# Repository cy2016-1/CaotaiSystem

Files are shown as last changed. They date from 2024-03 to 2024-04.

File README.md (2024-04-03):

# CaotaiSystem

### 介绍
一只会走路、会跳舞、会写字的草太椅子     
[视频介绍求三连](https://www.bilibili.com/video/BV1XD42157Rq/)     

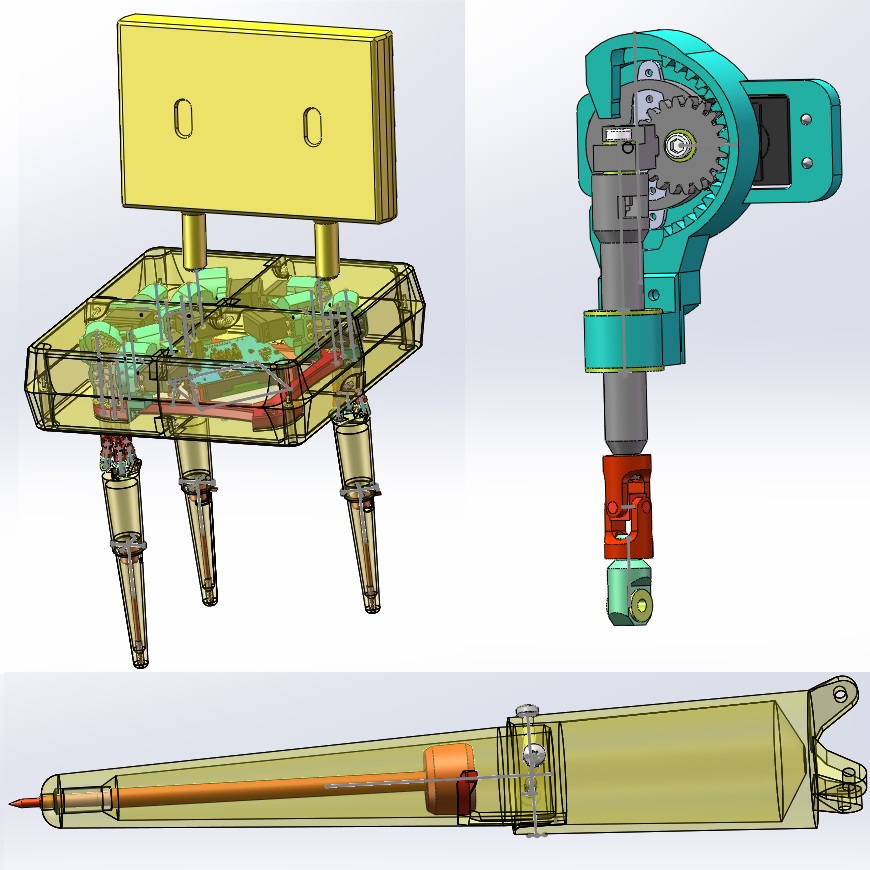
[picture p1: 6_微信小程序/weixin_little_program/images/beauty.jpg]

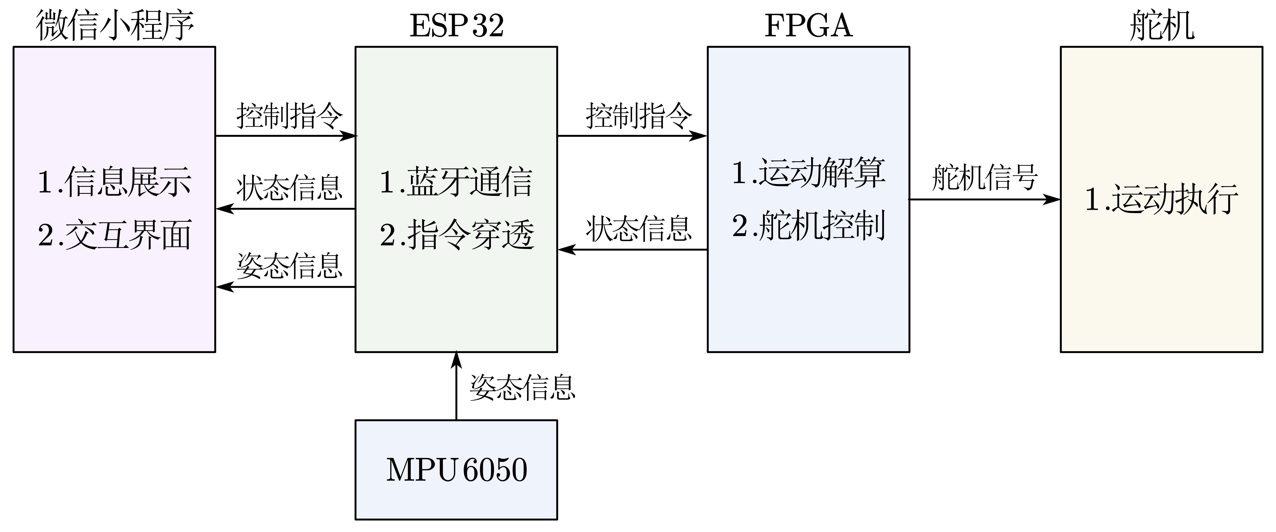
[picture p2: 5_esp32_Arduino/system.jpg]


### 文件内容

##### 1_结构

这个文件夹里放了草太椅子机械结构相关的文件
1.  `草太椅子`文件夹是椅子主体，使用SOLIDWORKS Premium 2021 SP5.0绘制，考虑到Solidworks向下兼容，所以应该使用同版本或更高版本打开
2.  `鞋子`文件夹放了三种鞋子，如果是走路功能，则使用`鞋子-前脚`和`鞋子-后脚`，如果是写字功能和跳舞功能，则换用`后脚-稳定站立`，因为稳定站立版本不容易前倾，所以摔倒风险会小一些，但是走路时难以向前移动重心
3.  `单轴往复运动STL`放了单轴往复子装配体的STL文件，可用于3D打印切片
4.  除了3D打印件以外，还要购买舵机、滑动轴承、肩轴螺丝等标准件，[草太结构标准件BOM.xlsx](1_结构/草太结构标准件BOM.xlsx)是物料清单

##### 2_电路

这个文件夹里放了电路板相关的文件
1.  `ProProject_caotai_ctrl_v2.epro`是嘉立创EDA pro另存为本地的工程文件，嘉立创EDA挺好用的，我已经从Cadence转到国产EDA了。打开步骤如下：     
（1）进入https://lceda.cn/ ，微信扫码登录     
（2）依次点开嘉立创EDA 编辑器 专业版，进入在线编辑器界面     
（3）点击文件->导入->嘉立创EDA专业版，在弹出的文件选择窗口选择`ProProject_caotai_ctrl_v2.epro`     
（4）等待导入完成，1分钟左右     
（5）在弹出的导入窗口中点击保存按钮，即可导入完成     
（6）点开PCB1，屏幕右上角有个类似购物车的图标，点击可以进入打样，下单之前别忘了领取1-4层板沉金免费券
2.  `草太控制板-电子元器件BOM.xlsx`是物料清单，都是正确的，大胆购买吧
3.  舵机不是纯阻性器件，会产生过冲电流，二极管`D2`和`D3`是瞬态抑制二极管，焊接时不可省略它们（血泪教训）

##### 3_算法

这个文件夹里放了算法相关的代码，是用了2个相互独立的全连接神经网络     
已知我们的草太椅子有4条腿，每条腿有3个伸缩连杆，我们算法的目的是解算出某个单腿姿态下3只伸缩连杆的高度，因为针对单条腿进行解算，没有把4条腿都联结起来，所以动作会有些生硬(T.T)     
第一个神经网络是2-64-64-2的结构，输入的2个神经元分别代表草太腿的外倾角和旋转角，输出的2个神经元分别代表伸缩连杆B、C和伸缩连杆A的高度之差     
第二个神经网络是3-64-64-64-3的结构，输入的3个神经元分别代表草太脚尖的x/y/z轴坐标，输出的3个神经元分别代表3只伸缩连杆的高度
1.  [dataset_angle.m](3_算法/dataset_angle.m)和[dataset_draw.m](3_算法/dataset_draw.m)分别用于生成上述两个神经网络的数据集，数据集是通过解方程组产生的，核心代码在[function_forward.m](3_算法/function_forward.m)里面
2.  [train_angle.ipynb](3_算法/train_angle.ipynb)和[train_draw.ipynb](3_算法/train_draw.ipynb)是训练这两个神经网络的代码，用到了`Tensorflow`框架
3.  [eval_angle.m](3_算法/eval_angle.m)和[eval_draw.m](3_算法/eval_draw.m)用于评估这两个神经网络的精度，包括浮点精度和在FPGA实现时的定点精度
4.  [make_para_rom.m](3_算法/make_para_rom.m)、[make_h2t_rom.m](3_算法/make_h2t_rom.m)和[make_sin_rom.m](3_算法/make_sin_rom.m)用于FPGA实现时生成相关的查找表文件

##### 4_FPGA

这个文件夹里放了FPGA的工程，使用安路FPGA开发工具[TD4.6.4](https://www.anlogic.com/support/tools-downloads)进行开发

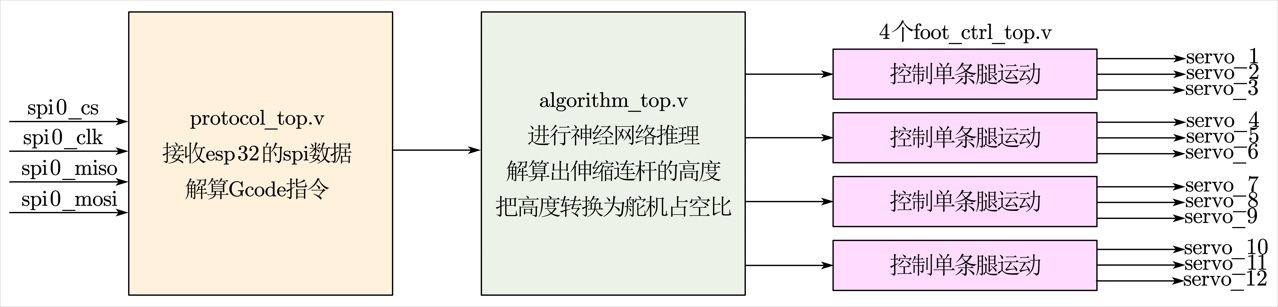
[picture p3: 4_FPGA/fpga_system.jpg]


##### 5_esp32_Arduino

这个文件夹里放了esp32的代码，主要完成2个功能：a.把从蓝牙收到的指令透传给FPGA；b.读取`mpu6050`的姿态
1.  使用`VS code`作为开发环境，`Arduino`作为框架来开发esp32
2.  在`PIO Home`新建工程，板卡选择`Espressif ESP32 Dev Module`，框架选择`Arduino`
3.  在`PIO Home`搜索`mpu6050`，在搜索到的库中选择`I2Cdevlib-MPU6050 by Jeff Rowberg`，add to project
4.  把本文件夹里的`main.cpp`作为工程的主函数编译、下载即可

##### 6_微信小程序

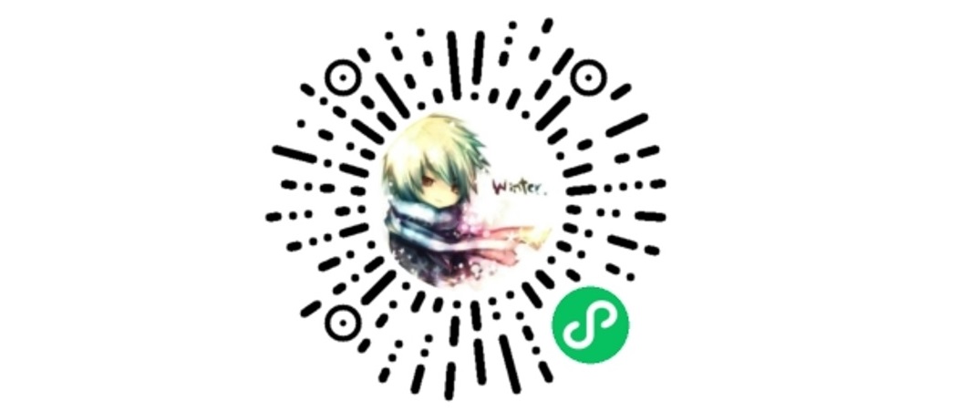
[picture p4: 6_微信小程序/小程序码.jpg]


草太椅子采用微信小程序作为上位机来进行控制，有3种方法打开
1.  微信首页搜索`上仙的蓝牙法器`即可在搜索的小程序结果中找到对应小程序
2.  扫描上面的小程序码可以进入小程序，我这个小程序已经走完ICP备案、微信认证、隐私合规流程了哦，是有编制的小程序哦
3.  把代码下载到本地，然后使用`微信开发者工具`自行编译，使用`真机调试`功能也可体验小程序

### 复刻说明

##### 如果你想完全复刻

1.  如果你想复刻这把椅子，建议从`单轴往复装配体`开始，该装配体实现了单轴的直线运动     
（1）采用了多处`滑动轴承`+`肩轴螺丝`+`M2.5螺母`的设计，安装时一只手用尖嘴钳夹紧`M2.5螺母`，另一只手用六角匙拧`肩轴螺丝`，注意拧得太紧会导致无法运动，拧得太松会导致公差过大，拧到连接处可以转动但又不会乱晃为止     
（2）安装舵机时，应把舵机调整到90°状态，必须把内齿轮安装在整个伸缩连杆行程的中间位置     
（3）3D打印时`伸缩连杆`卧倒打印，这样会使打印的层纹平行于连杆，从而增加结构强度，如果强度太弱会导致和万向节连接处发生断裂
2.  接下来是制作`草太的腿`装配体，把`新的小腿`、`大腿`、`腿的按钮`、`0.5*6*25弹簧`、`花枝俏毛笔`组装在一起
3.  `单轴往复装配体`和`草太的腿`调试完成后，把`十二轴连接器`打印出来，安装在一起，构成草太椅子的主体

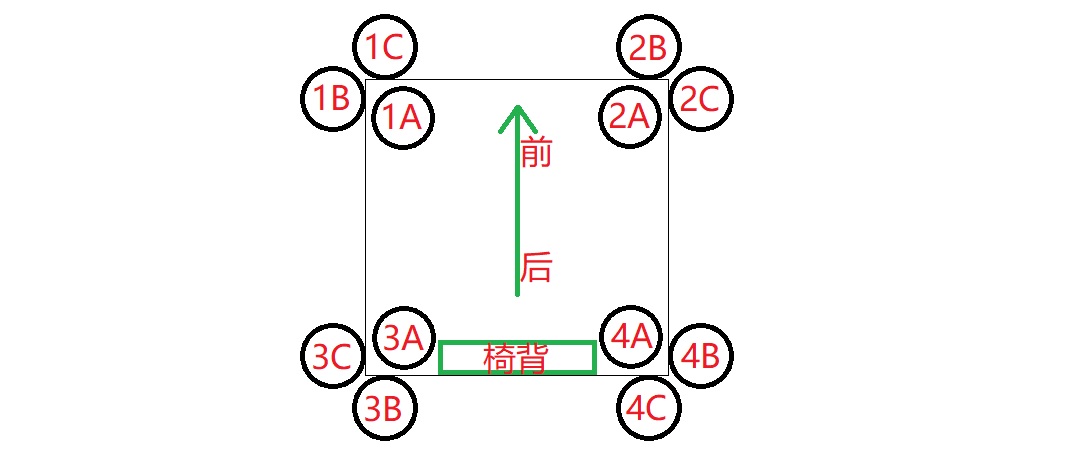
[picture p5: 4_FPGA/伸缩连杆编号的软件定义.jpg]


4.  电路板打样，esp32和FPGA程序烧录，把舵机出线插在电路板上，插线定义参见上图
5.  打印`椅子的顶面`、`椅子的底面`和`椅背`，这三个零件边长30cm左右，如果你的打印机没有这么大，可以把它切分成4块分别打印，然后用螺丝紧固在一起，把上述零件组装在一起，至此结构和电路部分完成
6.  校正！这是最重要的一步，因为即使同一家购买的同一批生产的舵机也难以做到完全一致，所以安装完成后需要手动校正，包括2个层面的校正     
（1）第一个层面是舵机级别的校正，通过不断调整[caotai_top.v](4_FPGA/caotai_v1_0_TangPrimer_EG4S20BG256/rtl/caotai_top.v)第99~110行BIAS参数，最终实现草太上电时4只脚都完全垂直于地面     
（2）第二个层面是整机级别的校正，通过调整微信小程序控制页面的`行走功能超参数`和`跳舞功能超参数`，最终实现草太可以稳定走路和跳舞而不摔倒
7.  最后，enjoy it!

##### 如果你想不完全复刻

1.  虽然完全按照本仓库的代码和图纸复刻出来这把草太椅子很有趣，但可能不适合所有人，甚至会因为我本人水平有限而限制到复刻者的发挥
2.  所以复刻者可以充分发挥自己的能力，对本设计进行魔改，从而提升性能，这也是开源社区存在的意义之一，我目前能想到的有以下几个方向：     
（1）结构方面，把电机改为步进电机，替换掉模拟舵机，模拟舵机的精度太差了     
（2）算法方面，把4条腿联动起来进行运动解算，从而使动作更加自然     
（3）算法方面，把mpu6050的姿态数据用于保持平衡，从而增加稳定性（目前已经可以把数据读出来并上传到小程序显示，但是没有进行处理）     
（4）电路和FPGA方面，替换掉已经停产的[Tang Primer](https://wiki.sipeed.com/hardware/zh/tang/Tang-primer/index.html)，使用在产的其他FPGA核心板，比如载有高云FPGA的[Tang Primer 20K](https://wiki.sipeed.com/hardware/zh/tang/tang-primer-20k/primer-20k.html)，注意核心板替换了以后PCB也要重新绘制哦     
（5）校正流程方面，目前进行舵机层面的校正时，每次都要修改`caotai_top.v`再重新编译下载FPGA固件，这太麻烦了，所以可以通过增加通信协议指令来在线校正     
（6）其他我没有想到的方向...
3.  至少你得把`单轴往复装配体`复刻出来，它的直线运动很有趣

##### 如果你不想复刻

1.  esp32和微信小程序采用蓝牙进行交互的部分，目前已经调试稳定，可以成为其他设计的参考
2.  去B站对应[视频](https://www.bilibili.com/video/BV1XD42157Rq/)下面给我点个一键三连吧

### 参考引用

1.  内摆线实现旋转运动转直线运动的原理参考了[这个视频](https://www.bilibili.com/video/BV1mZ4y1f7oy/)
2.  esp32和微信小程序通过蓝牙进行通信参考了[这个视频](https://www.bilibili.com/video/BV1oq4y1q7sC/)

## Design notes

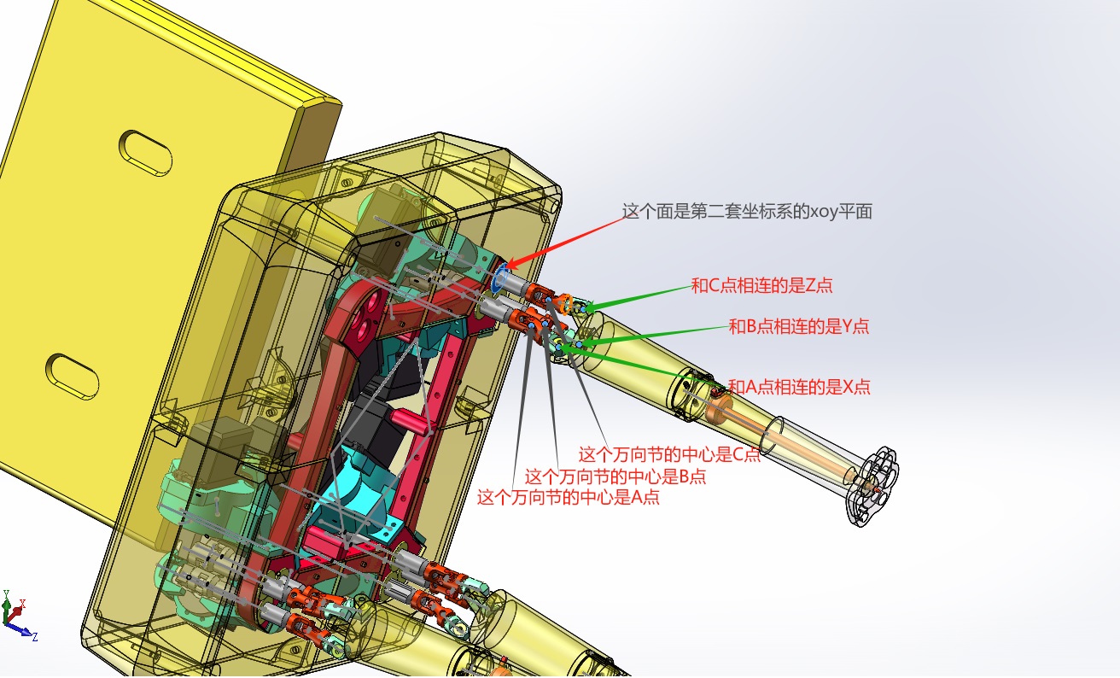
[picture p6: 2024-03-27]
3_算法/点和坐标系定义.jpg

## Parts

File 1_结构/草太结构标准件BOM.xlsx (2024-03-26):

B站 镇元上仙
会动的椅子——草太——结构标准件——Bill of Material
序号 | 在Solidworks中的零件名称 | 购买链接 | 备注 | 单价（￥） | 数量 | 小计（￥）
1 | 大舵机装配体[阿奇设计分享提供]2018 | https://item.taobao.com/item.htm?_u=k2gd4l1n6218&id=561100287559&skuId=3895267604718 | MG996（180度） 从Solidworks里来看似乎“人字-外齿轮-下半部分”零件和舵机有干涉，但请不要担心，因为这家的舵机伸出来的齿比其他家高1mm，你直接打印是正常安装的。 反而，如果你是从其他家买的MG996舵机，有可能需要把“人字-外齿轮-下半部分”零件的最后一个拉伸特征压缩掉才能正常安装 | 11.3 | 12 | 135.6
2 | 易格斯轴承GFM-0304-03 2018 | https://item.taobao.com/item.htm?_u=k2gd4l1nc5a5&id=521900618739&skuId=4980660613011 | 【深灰色.GFM-0304-03】 | 1.4 | 96 | 134.4
3 | 易格斯轴承GFM-1012-06 2018 | https://item.taobao.com/item.htm?_u=k2gd4l1nc5a5&id=521900618739&skuId=4471247887801 | 【深灰色.GFM-1012-06】 | 1.9 | 24 | 45.6
4 | ￠4×M2.5×12 轴肩螺丝 2018 | https://detail.tmall.com/item.htm?_u=k2gd4l1n0a79&id=707426540596&skuId=4973875173715 | 光杆3*12*M2.5(10个) 实际上件48只 | 3.06 | 5 | 15.3
5 | GB／T6172．2-2000非金属嵌件六角锁紧薄螺母2.5 | https://detail.tmall.com/item.htm?_u=k2gd4l1neae7&id=40325857988&skuId=4936608260655 | M2.5(50个)304 实际上件48只 | 6.44 | 1 | 6.44
6 | 万向节6x6装配体 | https://item.taobao.com/item.htm?_u=k2gd4l1n025f&id=521191969211&skuId=3105568646917 | 6*6MM万向节 | 2.8 | 12 | 33.6
7 | GB845-1985十字槽盘头自攻螺钉-C型ST2．9×12 | https://detail.tmall.com/item.htm?_u=k2gd4l1ne507&id=626324857641&skuId=5310338114487 | M3*12【50只】 实际上件98只 | 2.5 | 2 | 5
8 | GB／T70．1-2000内六角圆柱头螺钉M3×12 | https://detail.tmall.com/item.htm?_u=k2gd4l1n1d74&id=634243832662&skuId=5440040927616 | M3*12（50个 实际上件12只 | 2.53 | 1 | 2.53 | 草太椅面的边长约30cm，而我的打印机最大只能打印20cm，所以我就把椅面分成了4块分别打印然后再用螺钉螺母拼接起来 这组螺钉螺母就是拼接椅面的4个part用的，如果你的打印机大于30厘米，这个就可以省掉啦
9 | GB／T6172．2-2000非金属嵌件六角锁紧薄螺母3 | https://detail.tmall.com/item.htm?_u=k2gd4l1neae7&id=40325857988&skuId=4936608260656 | M3(50个)304 实际上件12只 | 3.24 | 1 | 3.24
10 | 大的压缩的弹簧 | https://detail.tmall.com/item.htm?_u=k2gd4l1n5679&id=640992562746&spm=a1z09.2.0.0.67002e8dteUE9g | 0.5*6*25mm 需要口头告诉客服这个尺寸，是定制的 | 4.5 | 1 | 4.5
11 | 笔芯 | https://detail.tmall.com/item.htm?_u=k2gd4l1n70f1&id=601808839108&skuId=4206044776631 | 花枝俏（小） | 6.6 | 1 | 6.6 | 本来想用按动笔笔芯的，但是公差太大无法演示写字功能，所以换成了软软的毛笔
12 | 椅背 | https://item.taobao.com/item.htm?_u=k2gd4l1n191b&id=38828402808&skuId=5209399448081 | 黄30*17*4.5厘米2张 草太4条腿站立没问题，但是如果抬起后面的一条腿，就会因为3D打印的椅背太重而重心太靠后而摔倒，所以在演示跳舞功能和走路功能时我把3D打印的椅背换成了泡沫椅背，从而减小了重量，减小了保持平衡的难度 | 16 | 1 | 16
13 |  |  |  |  | 总计 | 408.81 | RMB
14
15
16
17
18
19
20
21
22
23
24
25
26
27

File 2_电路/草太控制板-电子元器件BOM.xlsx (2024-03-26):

No. | Quantity | Designator | Comment | 购买链接 | 备注 | 单价￥ | 小计￥
1 | 7 | C1,C2,C9,C13,C14,C23,C40 | 47uF | https://item.taobao.com/item.htm?_u=l2gd4l1n249c&id=651730279981&skuId=4866792818122 | 47UF 25V尺寸：0603（100只） | 0.1 | 0.7
2 | 11 | C3,C10,C15,C22,C24,C26,C31,C36,C38,C41,C42 | 10uF | https://item.taobao.com/item.htm?_u=l2gd4l1n249c&id=651730279981&skuId=4866792818110 | 10UF 25V尺寸：0603（100只） | 0.04 | 0.44
3 | 13 | C4,C5,C11,C16,C17,C21,C25,C27,C30,C34,C35,C37,C39 | 0.1uF | https://item.taobao.com/item.htm?_u=l2gd4l1n175a&id=568023887250&skuId=3790413719806 | 0，1UF 104 | 0.04 | 0.52
4 | 2 | C6,C18 | 2.2nF | https://detail.tmall.com/item.htm?_u=l2gd4l1nf8c8&id=611226763970&skuId=4468071918326 | 0603 2.2NF ±10% 50V（50只） | 0.04 | 0.08
5 | 2 | C7,C19 | 22pF | https://detail.tmall.com/item.htm?_u=l2gd4l1nb44e&id=610747185789&skuId=4300586341508 | 0603 22PF 5% 50V（50只） | 0.08 | 0.16
6 | 2 | C8,C20 | 0.01uF | https://item.taobao.com/item.htm?_u=l2gd4l1n175a&id=568023887250&skuId=3790413719805 | 0，01UF 103 | 0.04 | 0.08
7 | 1 | C12 | 470uF | https://detail.tmall.com/item.htm?_u=l2gd4l1nbf3d&id=608506860246&skuId=4449283259604 | 470UF 50V绿金高频10*20 10只 | 0.38 | 0.38
8 | 1 | C28 | 1uF | https://item.taobao.com/item.htm?_u=l2gd4l1n249c&id=651730279981&skuId=4866792818086 | 1UF 50V尺寸：0603（100只） | 0.04 | 0.04
9 | 3 | D1,D2,D3 | SMBJ24CD-M3/I | https://detail.tmall.com/item.htm?_u=l2gd4l1nb88d&id=709925638952&skuId=5148547086648 | SMBJ6.5A/KK单向（20个） | 0.09 | 0.27
10 | 2 | H3,H4 | HDR-F_2.54_1x20P | https://detail.tmall.com/item.htm?_u=l2gd4l1nde67&id=607373839301&skuId=4255759944279 | 20P单排（10只） | 0.25 | 0.5
11 | 4 | H5,H6,H7,H8 | HDR-M_2.54_2x6 | https://detail.tmall.com/item.htm?_u=l2gd4l1n6acf&id=613869696323&skuId=4324124816160 | 2*6P 直针 铜（20条） | 0.16 | 0.64
12 | 1 | H9 | B-2100S08P-A110 | https://detail.tmall.com/item.htm?_u=l2gd4l1nad2a&id=615605943029&skuId=5048123656390 | MPU6050模块 黄色钽电容 镀金板 | 8.8 | 8.8
13 | 2 | L1,L2 | 4.7uH | https://detail.tmall.com/item.htm?_u=l2gd4l1n014e&id=607797277916&skuId=4265923664938 | CDRH104R 4.7UH(4R7) 5只 | 0.4 | 0.8
14 | 2 | Q1,Q2 | SS8050-H | https://detail.tmall.com/item.htm?_u=l2gd4l1n1e24&id=621537643738&skuId=4693769020834 | SS8050 SOT23 印字Y1 贴片（50个） | 0.02 | 0.04
15 | 2 | R1,R6 | 100K | https://detail.tmall.com/item.htm?_u=l2gd4l1nbe1d&id=529532295464&skuId=3924853511284 | 100K 1% （100个） | 0.03 | 0.06
16 | 4 | R2,R3,R7,R8 | 43K | https://detail.tmall.com/item.htm?_u=l2gd4l1nbe1d&id=529532295464&skuId=4880421480034 | 43K 1% （100个） | 0.03 | 0.12
17 | 5 | R4,R9,R11,R12,R13 | 10K | https://detail.tmall.com/item.htm?_u=l2gd4l1nef42&id=692806644853&skuId=4923889453118 | 0603 10K（100只） | 0.02 | 0.1
18 | 2 | R5,R10 | 1.6K | https://detail.tmall.com/item.htm?_u=l2gd4l1nef42&id=692806644853&skuId=4923889453092 | 0603 1.6K（100只） | 0.02 | 0.04
19 | 2 | R14,R15 | 5.1K | https://detail.tmall.com/item.htm?_u=l2gd4l1nef42&id=692806644853&skuId=4923889453108 | 0603 5.1K（100只） | 0.02 | 0.04
20 | 2 | R16,R17 | 4.7K | https://detail.tmall.com/item.htm?_u=l2gd4l1nbe1d&id=529532295464&skuId=3924853511210 | 4.7K 1% （100个） 无需上件 | 0.03 | 0.06
21 | 27 | R18,R19,R20,R21,R22,R23,R24,R25,R26,R27,R28,R29,R30,R31,R32,R33,R34,R35,R36,R37,R38,R39,R40,R41,R42,R43,R44 | 22 | https://detail.tmall.com/item.htm?_u=l2gd4l1nbe1d&id=529532295464&skuId=3924853511182 | 22欧 1% (100个) | 0.03 | 0.81
22 | 1 | R45 | 0 | https://detail.tmall.com/item.htm?_u=l2gd4l1n1e36&id=609667022770&skuId=4451493542761 | 0603 0R欧姆1% 100个 无需上件 | 0.03 | 0.03
23 | 1 | U1 | 3节18650电池盒插针 | https://item.taobao.com/item.htm?_u=l2gd4l1n4af0&id=706460008309&skuId=4965677504942 | 3节18650 硬壳 插针 1个 | 3.2 | 3.2
24 | 4 | U2,U5,U7,U16 | 1N5824 | https://detail.tmall.com/item.htm?_u=l2gd4l1nd759&id=14947051899&skuId=4174373459142 | SS54二极管 1N5824 5A/40V DO-214AC/SMA(10个） | 0.39 | 1.56
25 | 1 | U3 | KCD11船型开关 | https://detail.tmall.com/item.htm?_u=l2gd4l1n3c8b&id=529061266965&skuId=3945699927565 | 2脚2档 红色 10x15mm（5个） | 0.46 | 0.46
26 | 2 | U4,U6 | TPS54531DDAR | https://item.taobao.com/item.htm?_u=l2gd4l1n941b&id=569649171844&spm=a1z09.2.0.0.1f7a2e8dEYwB9l | tps54531 | 1.45 | 2.9
27 | 1 | U8 | AMS1117-3V3 | https://detail.tmall.com/item.htm?_u=l2gd4l1n0514&id=13763392732&skuId=4172153575113 | AMS1117-3.3V 封装SOT89（10个） | 0.32 | 0.32
28 | 1 | U9 | ESP32-S | https://item.taobao.com/item.htm?_u=l2gd4l1nd17b&id=634424428305&skuId=4543431189229 | ESP32-WROOM-32E(16MB) | 19.5 | 19.5
29 | 1 | U10 | CH340C | https://item.taobao.com/item.htm?_u=l2gd4l1ndf89&id=575878939854&skuId=5125097058072 | CH340C | 1.65 | 1.65
30 | 1 | U11 | 20009-UCAF001-X | https://detail.tmall.com/item.htm?_u=l2gd4l1n7eec&id=712263210606&skuId=4986402848290 | USB/TYPE-C-16P/不带弹片/高品质(10个） | 0.35 | 0.35
31 | 1 | U15 | AMS1117-5V0 | https://detail.tmall.com/item.htm?_u=l2gd4l1n0514&id=13763392732&skuId=4172153575113 | AMS1117-5.0V 封装SOT89（10个） | 0.32 | 0.32
 |  |  |  |  |  | 总计 | 44.97 | RMB

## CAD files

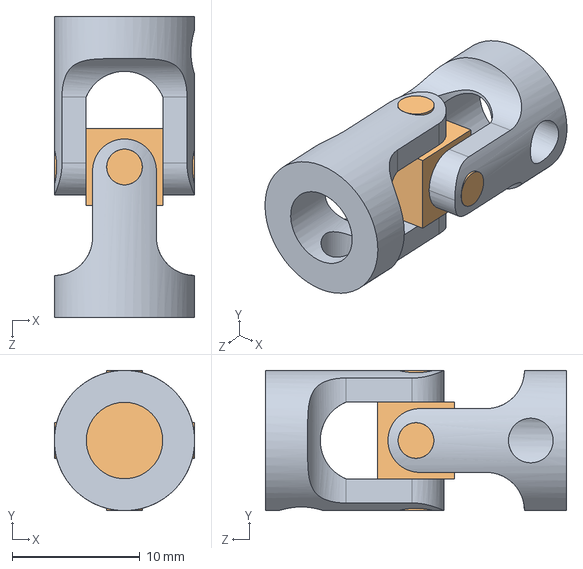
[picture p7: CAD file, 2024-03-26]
1_结构/草太椅子/万向节6x6装配体.SLDASM
11.0 x 11.0 x 23.6 mm
万向节6x6连接件 x 2
万向节6x6中间件

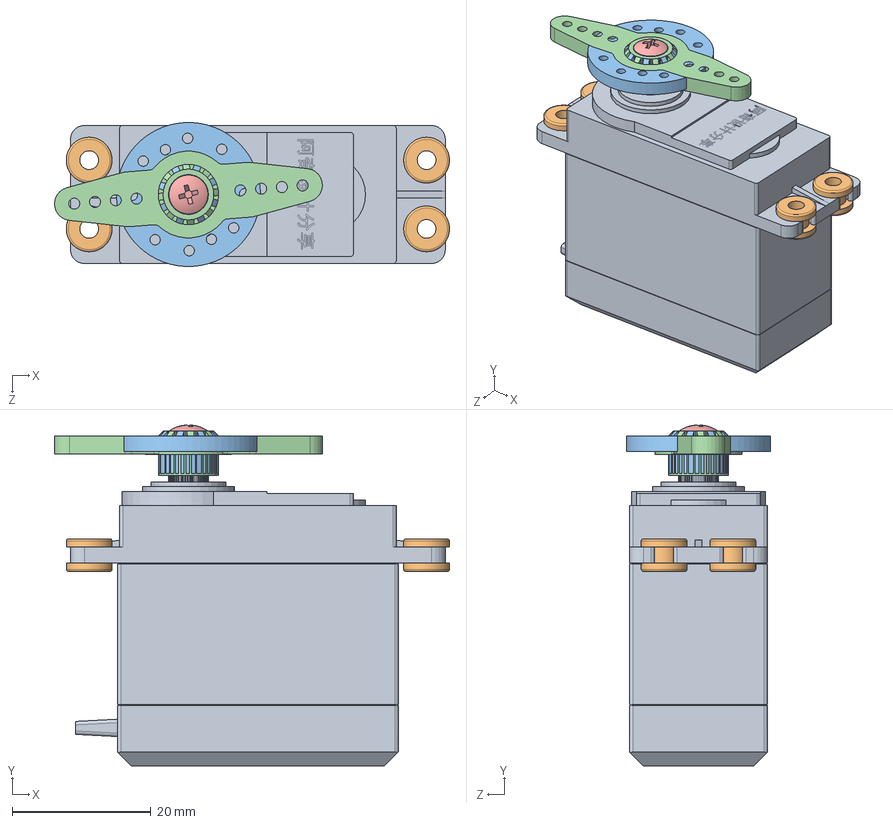
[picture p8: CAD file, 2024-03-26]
1_结构/草太椅子/大舵机装配体[阿奇设计分享提供]2018.SLDASM
56.9 x 49.1 x 20.7 mm
大舵机渲染2018
舵机橡胶圈渲染2018 x 4
舵机圆舵盘渲染2018
舵机单臂舵盘渲染2018
cross recessed pan head screws gb(GB_CROSS_SCREWS_TYPE1 M3X6-6 H type-N)2018

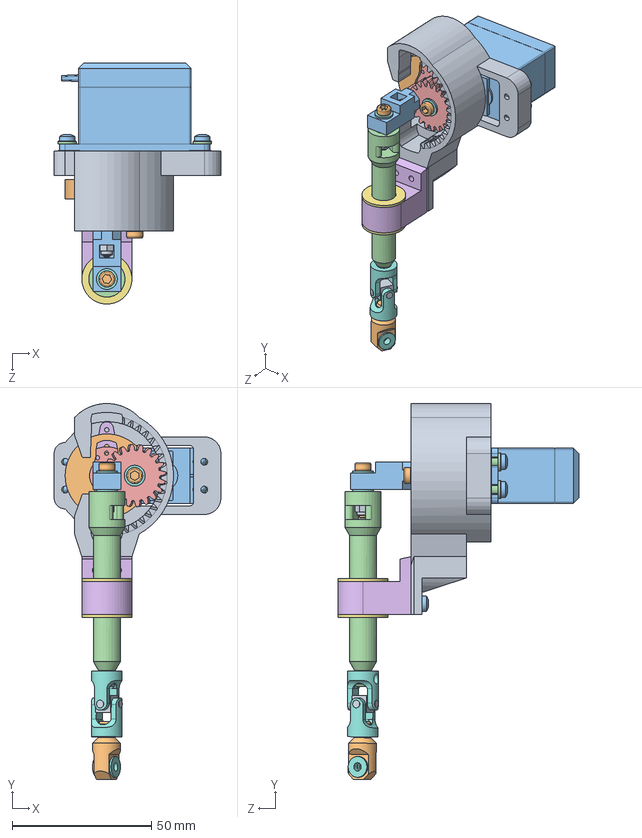
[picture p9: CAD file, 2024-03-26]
1_结构/草太椅子/单臂往复装配体.SLDASM
60.0 x 135.1 x 86.7 mm
人字-外齿轮-下半部分
内外齿轮连杆
大舵机渲染2018
舵机橡胶圈渲染2018 x 4
舵机单臂舵盘渲染2018
cross recessed pan head screws gb(GB_CROSS_SCREWS_TYPE1 M3X6-6 H type-N)2018
易格斯轴承GFM-0304-03 2018 x 8
GB／T6172．2-2000非金属嵌件六角锁紧薄螺母2.5 x 3
￠4×M2.5×12 轴肩螺丝 2018 x 3
直角连杆
伸缩连杆
人字-内齿轮
人字-外齿轮-上半部分
易格斯轴承GFM-1012-06 2018 x 2
万向节6x6连接件 x 2
万向节6x6中间件
大腿连杆
GB845-1985十字槽盘头自攻螺钉-C型ST2．9×12 x 6

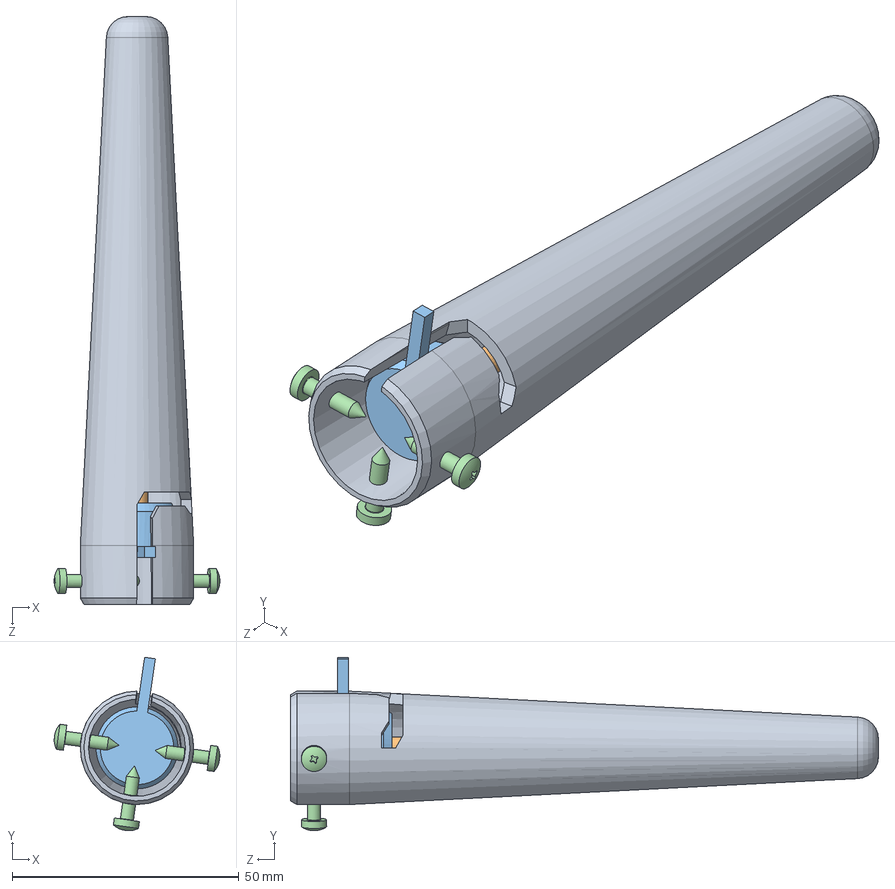
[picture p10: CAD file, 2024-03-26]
1_结构/草太椅子/草太的腿.SLDASM
36.5 x 38.2 x 129.6 mm
新的小腿
笔芯
腿的按钮
GB845-1985十字槽盘头自攻螺钉-C型ST2．9×12 x 3

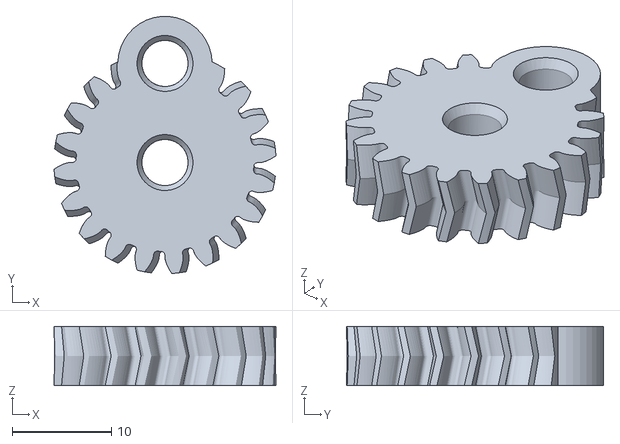
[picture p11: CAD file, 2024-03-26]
1_结构/单轴往复运动STL/人字-内齿轮.STL
22.4 x 25.9 x 6.00

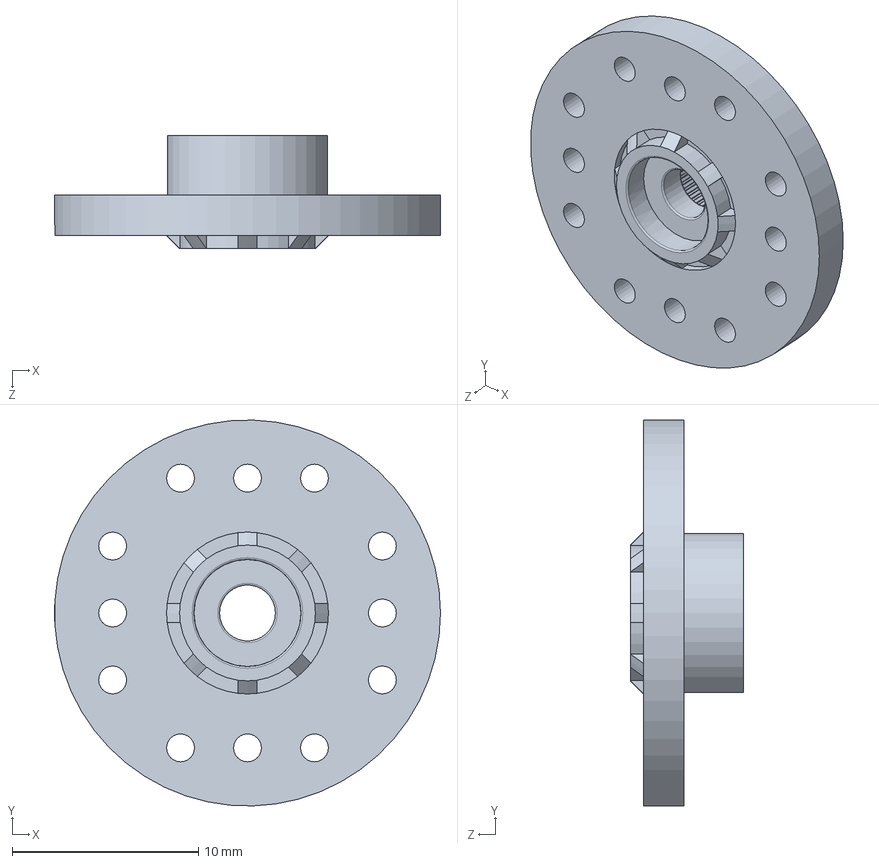
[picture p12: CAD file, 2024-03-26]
1_结构/草太椅子/舵机圆舵盘渲染2018.sldprt
20.8 x 20.7 x 6.10 mm

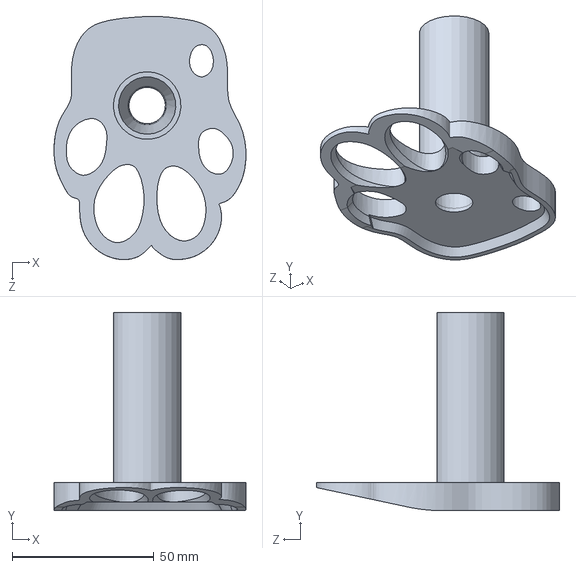
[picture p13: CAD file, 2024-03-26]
1_结构/鞋子/鞋子-后脚.SLDPRT
67.8 x 70.0 x 85.9 mm

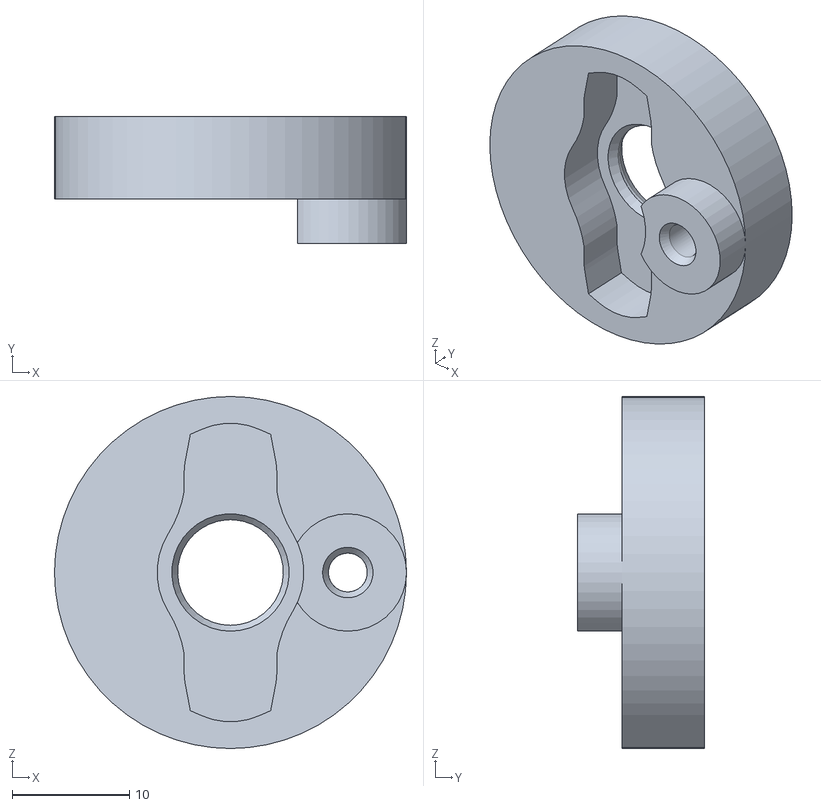
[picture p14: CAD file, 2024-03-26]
1_结构/单轴往复运动STL/内外齿轮连杆.STL
30.0 x 10.8 x 30.0

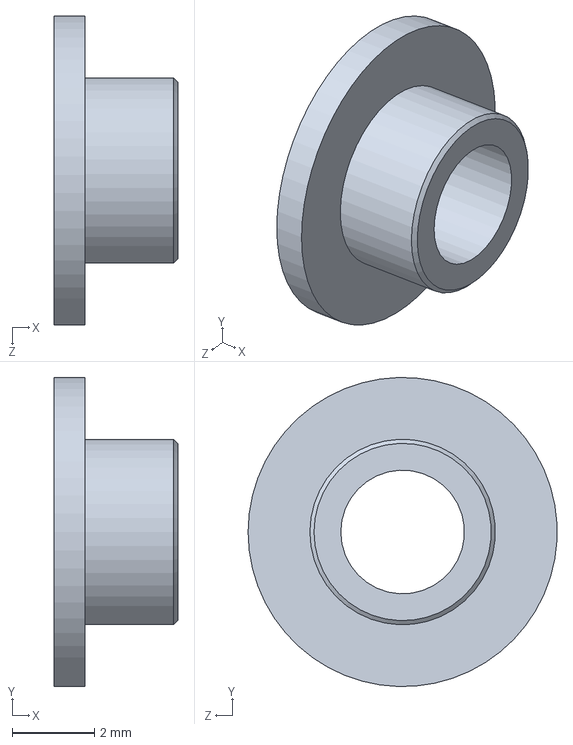
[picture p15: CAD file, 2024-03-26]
1_结构/草太椅子/易格斯轴承GFM-0304-03 2018.SLDPRT
3.00 x 7.50 x 7.49 mm

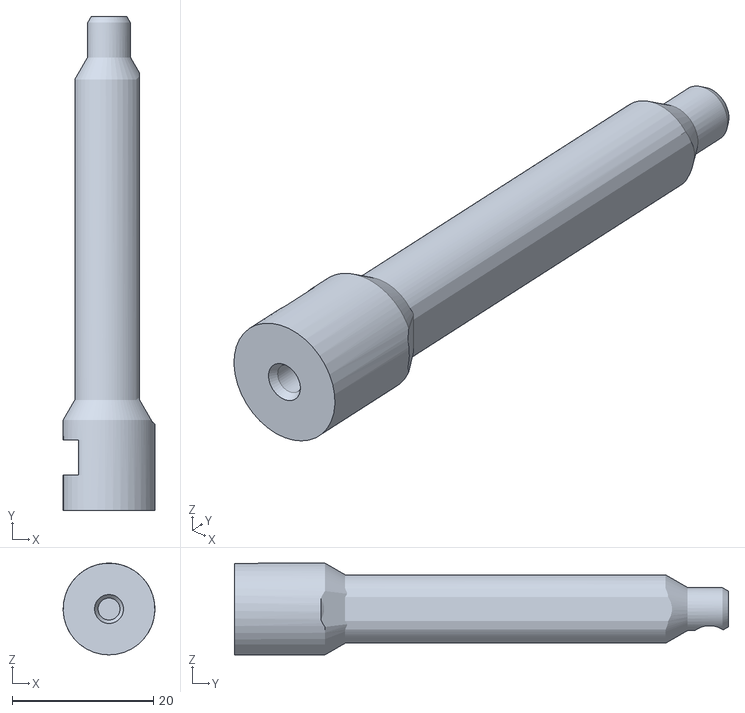
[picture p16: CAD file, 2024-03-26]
1_结构/单轴往复运动STL/伸缩连杆.STL
13.0 x 70.0 x 13.0

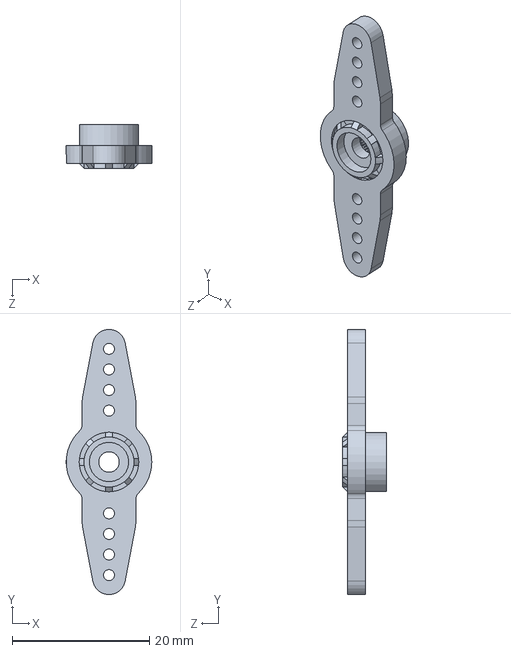
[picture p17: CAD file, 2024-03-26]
1_结构/草太椅子/舵机单臂舵盘渲染2018.sldprt
12.5 x 38.7 x 6.35 mm

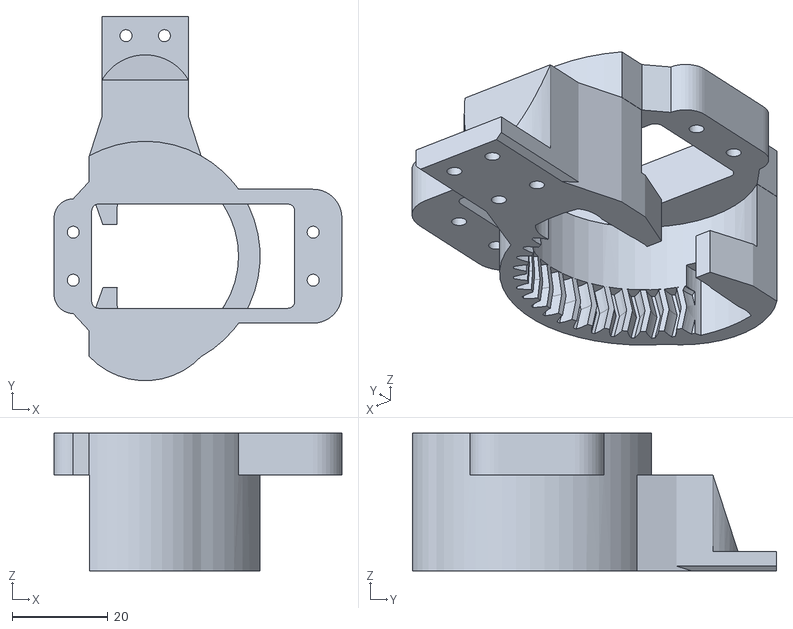
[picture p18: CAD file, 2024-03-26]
1_结构/单轴往复运动STL/人字-外齿轮-下半部分.STL
60.0 x 75.9 x 28.7

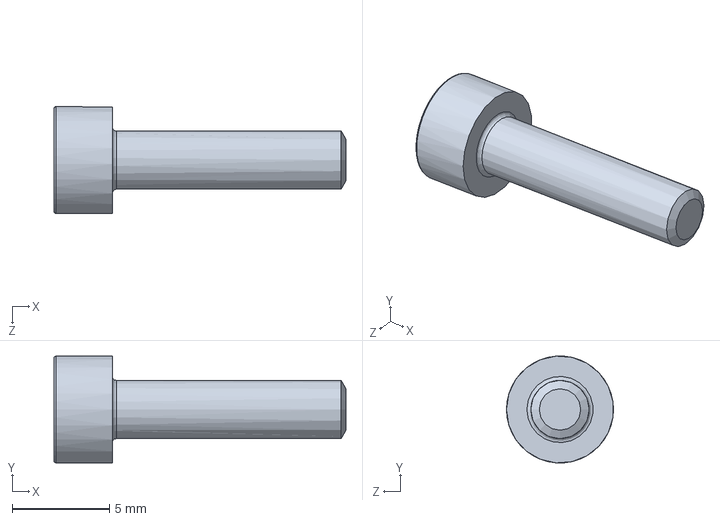
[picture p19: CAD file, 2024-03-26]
1_结构/草太椅子/GB／T70．1-2000内六角圆柱头螺钉M3×12.SLDPRT
15.0 x 5.48 x 5.50 mm

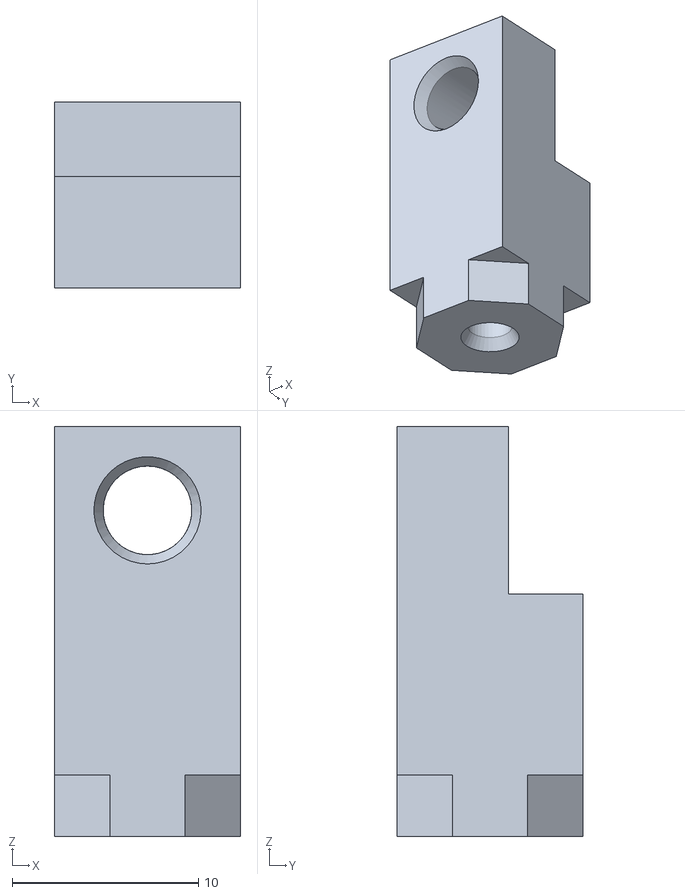
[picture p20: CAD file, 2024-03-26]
1_结构/单轴往复运动STL/直角连杆.STL
10.0 x 10.0 x 22.0

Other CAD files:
1_结构/鞋子/鞋子-后脚-稳定站立.SLDPRT
1_结构/鞋子/鞋子-前脚.SLDPRT
1_结构/草太椅子/易格斯轴承GFM-1012-06 2018.SLDPRT
1_结构/单轴往复运动STL/人字-外齿轮-上半部分.STL
1_结构/草太椅子/GB845-1985十字槽盘头自攻螺钉-C型ST2．9×12.SLDPRT
1_结构/草太椅子/GB／T6172．2-2000非金属嵌件六角锁紧薄螺母2.5.SLDPRT
1_结构/草太椅子/GB／T6172．2-2000非金属嵌件六角锁紧薄螺母3.SLDPRT
1_结构/草太椅子/cross recessed pan head screws gb(GB_CROSS_SCREWS_TYPE1 M3X6-6 H type-N)2018.sldprt
1_结构/草太椅子/万向节6x6中间件.SLDPRT
1_结构/草太椅子/万向节6x6连接件.SLDPRT
1_结构/草太椅子/人字-外齿轮-上半部分.SLDPRT
1_结构/草太椅子/人字-外齿轮-下半部分.SLDPRT
1_结构/草太椅子/伸缩连杆.SLDPRT
1_结构/草太椅子/内外齿轮连杆.SLDPRT
1_结构/草太椅子/十二轴连接器.SLDPRT
1_结构/草太椅子/大的压缩的弹簧.SLDPRT
1_结构/草太椅子/大腿连杆.SLDPRT
1_结构/草太椅子/大腿部件.SLDPRT
1_结构/草太椅子/大舵机渲染2018.sldprt
1_结构/草太椅子/新的小腿.SLDPRT
1_结构/草太椅子/椅子的底面.SLDPRT
1_结构/草太椅子/椅子的底面_partA.SLDPRT
1_结构/草太椅子/椅子的底面_partB.SLDPRT
1_结构/草太椅子/椅子的底面_partC.SLDPRT
1_结构/草太椅子/椅子的底面_partD.SLDPRT
1_结构/草太椅子/椅子的顶面.SLDPRT
1_结构/草太椅子/椅子的顶面_partA.SLDPRT
1_结构/草太椅子/椅子的顶面_partB.SLDPRT
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

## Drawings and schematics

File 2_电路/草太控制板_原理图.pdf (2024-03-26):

# 电池盒

# 第一只TPS54531

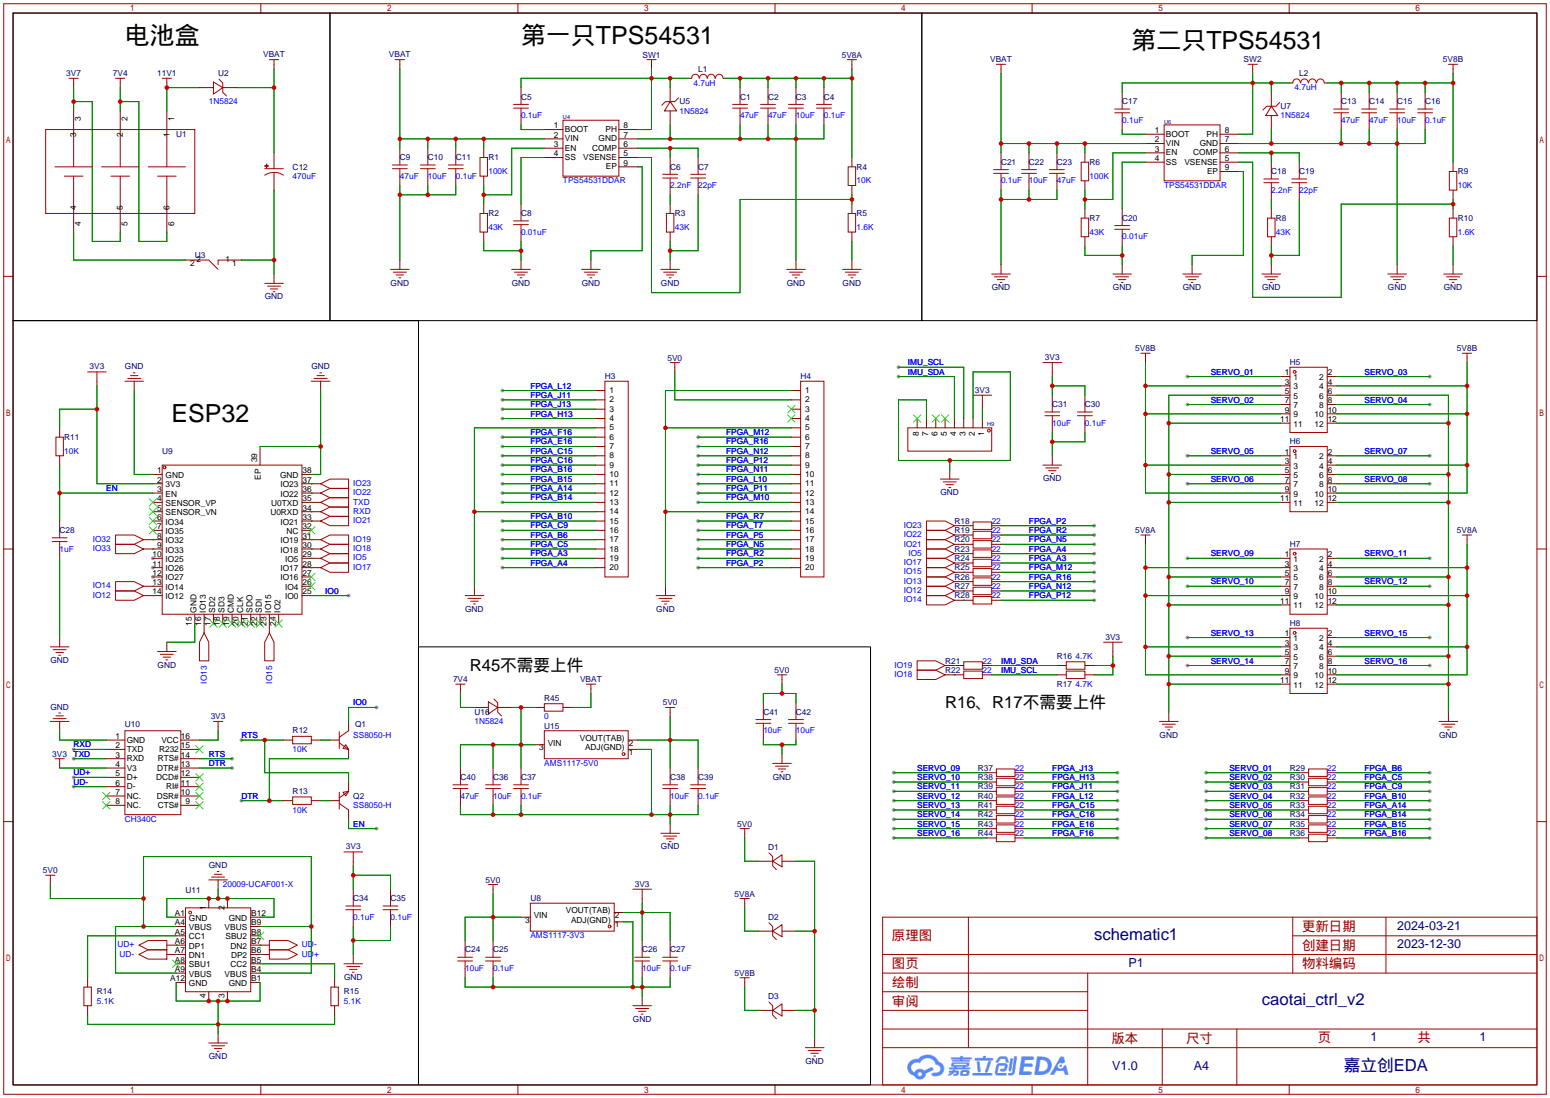
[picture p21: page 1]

GND B1 GND A12 VBUS A9 SBU1 A8 DN1 A7 DP1 A6 CC1 A5 VBUS A4 GND A1

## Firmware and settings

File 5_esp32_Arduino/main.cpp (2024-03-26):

#include <Arduino.h>
#include <BLEDevice.h>
#include <BLEServer.h>
#include <BLEUtils.h>
#include <BLE2902.h>
#include <iostream>
#include <SPI.h>
#include "I2Cdev.h"
#include "Wire.h"
#include "MPU6050_6Axis_MotionApps20.h"
// 宏定义
#define IMU_I2C_SDA 19 
#define IMU_I2C_SCL 18
#define PIN_CS0 15
#define FPGA_RSTN 17
#define FOOT_BACKPRESS 5
#define FOOT_BUSYSTATE 21
#define SERVICE_UUID "12a59900-17cc-11ec-9621-0242ac130002" // UART service UUID
#define CHARACTERISTIC_UUID_RX "12a59e0a-17cc-11ec-9621-0242ac130002"
#define CHARACTERISTIC_UUID_TX "12a5a148-17cc-11ec-9621-0242ac130002"
#define NOTIFY_LEN 10
#define QUEUE_LEN 32768


// BLE things
uint32_t ble_notify_cnt = 0;
uint32_t heartCount = 0;
uint8_t  broadcastValue[NOTIFY_LEN];
BLEServer *pServer = NULL;                   // BLEServer指针 pServer
BLECharacteristic *pTxCharacteristic = NULL; // BLECharacteristic指针 pTxCharacteristic
BLECharacteristic *pRxCharacteristic = NULL;
bool deviceConnected = false;                // 本次连接状态
bool oldDeviceConnected = false;             // 上次连接状态
uint8_t cmd_err_num = 0;
// mpu things
MPU6050 mpu;
bool dmpReady = false;  // set true if DMP init was successful
uint8_t mpuIntStatus;   // holds actual interrupt status byte from MPU
uint8_t devStatus;      // return status after each device operation (0 = success, !0 = error)
uint16_t packetSize;    // expected DMP packet size (default is 42 bytes)
uint16_t fifoCount;     // count of all bytes currently in FIFO
uint8_t fifoBuffer[64]; // FIFO storage buffer
Quaternion q;           // [w, x, y, z]         quaternion container
VectorInt16 aa;         // [x, y, z]            accel sensor measurements
VectorInt16 aaReal;     // [x, y, z]            gravity-free accel sensor measurements
VectorInt16 aaWorld;    // [x, y, z]            world-frame accel sensor measurements
VectorFloat gravity;    // [x, y, z]            gravity vector
float euler[3];         // [psi, theta, phi]    Euler angle container
float ypr[3];           // [yaw, pitch, roll]   yaw/pitch/roll container and gravity vector
uint8_t teapotPacket[14] = { '$', 0x02, 0,0, 0,0, 0,0, 0,0, 0x00, 0x00, '\r', '\n' };


class CircularQueue {
private:
  int front, rear;
  int capacity;
  uint8_t* queue;
public:
  CircularQueue(int k) {
    capacity = k + 1;
    queue = new uint8_t[capacity];
    front = rear = 0;
  }
  void enQueue(uint8_t value) {
    queue[rear] = value;
    rear = (rear + 1) % capacity;
  }
  uint8_t deQueue() {
    uint8_t ddd = queue[front];
    front = (front + 1) % capacity;
    return ddd;
  }
  bool isEmpty() {
    return rear == front;
  }
  bool isFull() {
    return (rear + 1) % capacity == front;
  }
  int getRear() {
    return rear;
  }
  int getFront() {
    return front;
  }
};

// 循环队列初始化
CircularQueue bleQueue(QUEUE_LEN);

class MyServerCallbacks : public BLEServerCallbacks
{
  void onConnect(BLEServer *pServer)
  {
    deviceConnected = true;
  };
  void onDisconnect(BLEServer *pServer)
  {
    deviceConnected = false;
  }
};

class MyCallbacks : public BLECharacteristicCallbacks
{
  void onWrite(BLECharacteristic *pCharacteristic)
  {
    Serial.printf("onWrite\n");
    std::string rxValue = pCharacteristic->getValue(); // 接收信息
    if (rxValue.length() > 0)
    {
      for (int i = 0; i < rxValue.length(); i++) {
        bleQueue.enQueue(rxValue[i]);
      }
    }
  }
};

void notifyWx() {
  int8_t temp = 0;
  if (!dmpReady) return;
  if (mpu.dmpGetCurrentFIFOPacket(fifoBuffer)) {
  mpu.dmpGetQuaternion(&q, fifoBuffer);
  mpu.dmpGetGravity(&gravity, &q);
  mpu.dmpGetYawPitchRoll(ypr, &q, &gravity);
    /*Serial.print("ypr\t");
    Serial.print(ypr[0] * 180/M_PI);
    Serial.print("\t");
    Serial.print(ypr[1] * 180/M_PI);
    Serial.print("\t");
    Serial.println(ypr[2] * 180/M_PI);*/
  }
  heartCount = heartCount + 1;
  for(int i=0;i<4;i++) {
    broadcastValue[NOTIFY_LEN-1-i] = static_cast<uint8_t>((heartCount>>(8*i)) & 255);
  }
  temp = (int8_t)(ypr[2] * 180/M_PI);
  if (temp<0) temp = temp + 256;
  for(int i=4;i<5;i++) {
    broadcastValue[NOTIFY_LEN-1-i] = static_cast<uint8_t>(temp & 255);
  }
  temp = (int8_t)(ypr[1] * 180/M_PI);
  if (temp<0) temp = temp + 256;
  for(int i=5;i<6;i++) {
    broadcastValue[NOTIFY_LEN-1-i] = static_cast<uint8_t>(temp & 255);
  }
  temp = (int8_t)(ypr[0] * 180/M_PI);
  if (temp<0) temp = temp + 256;
  for(int i=6;i<7;i++) {
    broadcastValue[NOTIFY_LEN-1-i] = static_cast<uint8_t>(temp & 255);
  }
  for(int i=7;i<8;i++) {
    broadcastValue[NOTIFY_LEN-1-i] = static_cast<uint8_t>(cmd_err_num);
  }
  Serial.printf("cmd_err_num is %d\n", cmd_err_num);
  for(int i=8;i<9;i++) {
    broadcastValue[NOTIFY_LEN-1-i] = static_cast<uint8_t>((digitalRead(FOOT_BACKPRESS)==1) ? 255 : 0);
  }
  for(int i=9;i<10;i++) {
    broadcastValue[NOTIFY_LEN-1-i] = static_cast<uint8_t>((digitalRead(FOOT_BUSYSTATE)==1) ? 255 : 0);
  }
  pTxCharacteristic->setValue(broadcastValue, NOTIFY_LEN);       // 设置要发送的值
  pTxCharacteristic->notify();              // 广播
}

void clearQueue() {
  if (bleQueue.isEmpty()) return;
  uint8_t ccc = 0;
  //Serial.printf("BLE RECV:");
  digitalWrite(PIN_CS0, LOW);
  while (!bleQueue.isEmpty()) {
    if (digitalRead(FOOT_BACKPRESS)==1) {
      Serial.println("FOOT_BACKPRESS==1");
      //Serial.printf("rear is %d, front is %d\n", bleQueue.getRear(), bleQueue.getFront());
      notifyWx();
      delay(1000);
      break;
    }
    ccc = bleQueue.deQueue();
    cmd_err_num = SPI.transfer(ccc);
    //Serial.printf("%c", ccc);
  }
  //Serial.println();
  digitalWrite(PIN_CS0, HIGH);
}

void serialISP() {
  uint8_t ccc = 0;
  if (Serial.available()>0) {
    Serial.printf("UART RECV:");
    digitalWrite(PIN_CS0, LOW);
    while (Serial.available()>0) {
      ccc = Serial.read();
      cmd_err_num = SPI.transfer(ccc);
      Serial.printf("%c", ccc);
    }
    Serial.println();
    digitalWrite(PIN_CS0, HIGH);
  }
}

void bleLoop() {
  // deviceConnected 已连接
  if (deviceConnected)
  {
    notifyWx();
  }
  // disconnecting  断开连接
  if (!deviceConnected && oldDeviceConnected)
  {
    delay(500);                  // 留时间给蓝牙缓冲
    pServer->startAdvertising(); // 重新广播
    Serial.println("BLE Restart Advertising");
    oldDeviceConnected = deviceConnected;
  }
  // connecting  正在连接
  if (deviceConnected && !oldDeviceConnected)
  {
    Serial.println("BLE Connect Successfully");
    // do stuff here on connecting
    oldDeviceConnected = deviceConnected;
  }
}

void bleSetup() {
  // 创建一个 BLE 设备
  BLEDevice::init("UART_BLE");
  // 创建一个 BLE 服务
  pServer = BLEDevice::createServer();
  pServer->setCallbacks(new MyServerCallbacks()); // 设置回调
  BLEService *pService = pServer->createService(SERVICE_UUID);
  // 创建一个 BLE 特征
  pTxCharacteristic = pService->createCharacteristic(CHARACTERISTIC_UUID_TX, BLECharacteristic::PROPERTY_NOTIFY);
  pTxCharacteristic->addDescriptor(new BLE2902());
  pRxCharacteristic = pService->createCharacteristic(CHARACTERISTIC_UUID_RX, BLECharacteristic::PROPERTY_WRITE);
  pRxCharacteristic->setCallbacks(new MyCallbacks()); // 设置回调
  // BLE开始
  pService->start();                  // 开始服务
  pServer->getAdvertising()->start(); // 开始广播
  Serial.println("BLE OK... ");
}

void mpuSetup() {
  Wire.begin(IMU_I2C_SDA, IMU_I2C_SCL);
  Wire.setClock(400000);
  mpu.initialize();
  Serial.println("Testing device connections...");
  Serial.println(mpu.testConnection() ? "MPU6050 connection successful" : "MPU6050 connection failed");
  mpu.setXGyroOffset(220);
  mpu.setYGyroOffset(76);
  mpu.setZGyroOffset(-85);
  mpu.setZAccelOffset(1788); // 1688 factory default for my test chip
  for (int k=0;k<4;k++) {
    Serial.printf("init dmp times: %d\n", k);
    mpu.setDMPEnabled(false);
    devStatus = mpu.dmpInitialize();
    mpu.CalibrateAccel(6);
    mpu.CalibrateGyro(6);
    mpu.setDMPEnabled(true);
  }
  Serial.println(devStatus ? "DMP initialize failed" : "DMP initialize success");
  dmpReady = devStatus ? false : true;
}

void setup() {
  // put your setup code here, to run once:
  pinMode(PIN_CS0, OUTPUT);
  pinMode(FPGA_RSTN, OUTPUT);
  pinMode(FOOT_BACKPRESS, INPUT);
  pinMode(FOOT_BUSYSTATE, INPUT);
  digitalWrite(FPGA_RSTN, LOW);
  // UART初始化
  Serial.begin(115200);
  Serial.printf("This is a caotai program\n");
  // SPI初始化
  SPI.begin(14,13,12,15); // sclk, miso, mosi, scs0
  SPI.setClockDivider(SPI_CLOCK_DIV8); // (1025-857)/7 = 24, 1707-857=850
  // BLE初始化
  bleSetup();
  digitalWrite(FPGA_RSTN, HIGH);
  delay(100);
  // MPU初始化
  mpuSetup();
}

void loop() {
  // receive uart char, then send to spi
  serialISP();
  // receive BLE char, then send to spi
  clearQueue();
  // read DMP, then notify to ble master
  if (ble_notify_cnt==499999) {
    bleLoop();
    ble_notify_cnt = 0;
  }
  else {
    ble_notify_cnt = ble_notify_cnt + 1;
  }
}

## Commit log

2024-03-26 首次提交
    [GB845-1985十字槽盘头自攻螺钉-C型ST2．9×12.SLDPRT, GB／T6172．2-2000非金属嵌件六角锁紧薄螺母2.5.SLDPRT, GB／T6172．2-2000非金属嵌件六角锁紧薄螺母3.SLDPRT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]
2024-03-27 增加文件介绍
2024-03-27 添加复刻说明
2024-03-27 修复已知bug
2024-03-28 增加复刻说明
2024-03-29 修改复刻说明
2024-03-30 增加B站视频链接
2024-04-03 优化文档描述
